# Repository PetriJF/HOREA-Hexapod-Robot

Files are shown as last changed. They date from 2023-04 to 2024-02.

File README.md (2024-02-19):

# ROS2 Hexapod (Major update coming up!!)
HOREA

## IMPORTANT: Code refactoring in progress

Hello everyone! Just letting you know that the code is currently being refactored for the robot. The Hardware design of the robot was simplified, making it easier to work with and even cheaper, and those changes need to be reflected into the walking model as well.
A quick list of some of the features in progress:
- [x] Dynamic Gait Switching
- [x] Leg Fault handling
- [ ] Gazebo integration (RViz is implemented, Gazebo comes next)
- [ ] Vision/LiDAR support (Progress was made but more is needed)
- [x] Better step feedback
- [x] Better femur design
- [x] Jumping
- [x] Enabling the hexapod to walk on 4 or 5 legs
- [ ] Enabling the hexapod to walk in a crawl state (reducing the profile widthwise for fitting into narrow spots)
- [x] A more efficient node communication method for the data heavy transfers
- [x] Battery support.
Once all of those are completed, the new update will be pushed and the repository will be cleaned.
Also, after this update, the project will move from an alpha-like phase to beta.

WHY NOT WORKING HERE?
Because I am using this version of the codebase for demos and project sharing. I don't want to add something that might be unstable or buggy here

WHEN WILL THE CHANGES BE UPLOADED?
My plan for it is to have the new hardware design uploaded by the end of December with the code changes required to run the software on it. All the other features should be online by late March 2024 when the private branch will be fully integrated with main.

SHOULD I BUILD THE CURRENT VERSION OF THE ROBOT?
Personally, I would say no, as the new version fixes a lot of the problems this iteration has. The new version will also be cheaper and easier to assemble and service! If you can't wait, email me at "jamespetri28@gmail.com" and we can work together for a quicker solution!

Thank you everyone,
James

## Project Description

As part of the Robotics and Intelligent Devices degree, in the final year a project has to be undertaken by each student.

For my final year project I chose to fully research, design and develeop a hexapod robot with the appropriate control strategy to traverse diffused terrain. I also wanted to apply best practices in order to maximize the quality of the robot while minimizing the price, as I would like to make it a good research and hobby platform for people to take and work with.

The Hexapod, named H.O.R.E.A., works on a raspberry Pi running ROS2 humble. It comes equipped with an IMU, for tilt correction, and a switch in each tibia, for leg feedback. With those two perception methods, the hexapod is fully prepared to undertake light to medium off-road challanges (Relative to the robot's size). Some metrics are available at the end.

In the future, the platform might add vision and a more robust control design in order to improve its capabilities even further.

## OPEN-SOURCE

Please note that the project is open-source, so feel free to fork it. I must mention that if you plan to work on the robot, please read the issues first as they might indicate a future feature I am working on that you might find useful. The project is work-in-progress, so it is worth checking it often for updates!

## CAD and 3D printing

The version current version of the hexapod is fully 3D printed in ABS, except for the TibiaTips, which are printed in TPU in order to provide more grip. Some images of the CAD assembly can be seen below

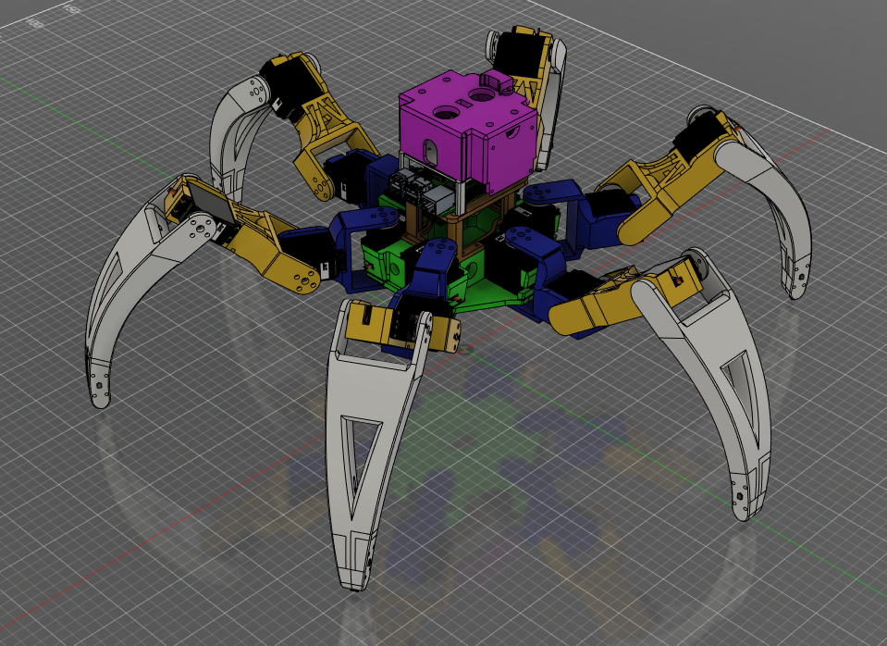
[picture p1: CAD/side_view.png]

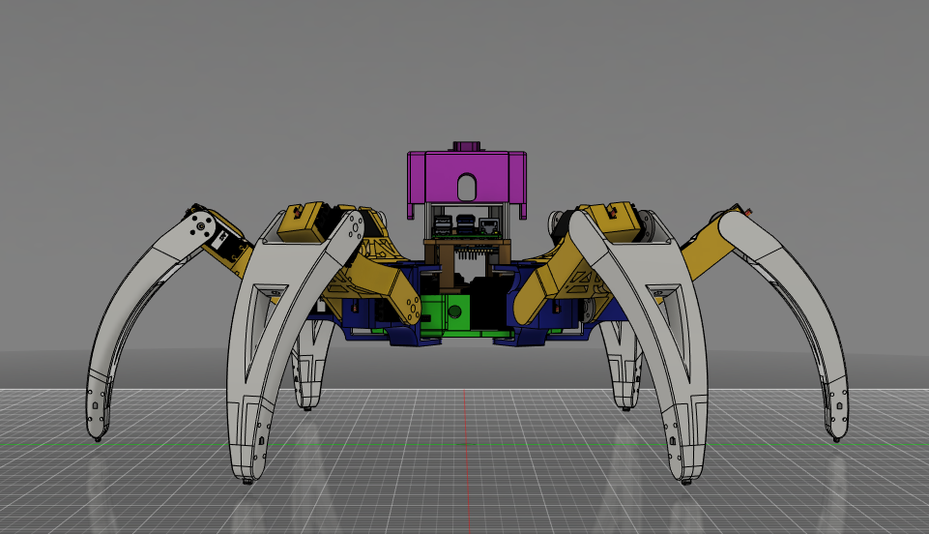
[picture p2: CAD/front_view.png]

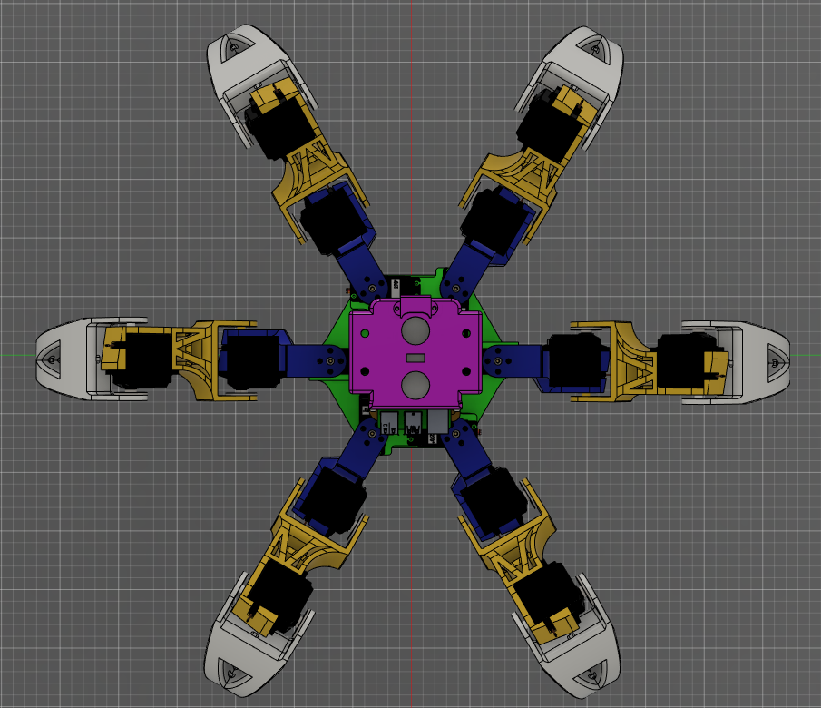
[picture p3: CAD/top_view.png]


## Codebase

The hexapod's codebase is designed to work with Ubuntu 22.04 Server and ROS2 Humble. I will not work on backwards compatibility with previous versions of ROS/Ubuntu. When cloning the repository, please ensure you properly install ROS2 Humble (do the talker listener demo to ensure so). Once cloned, go to the parent directory and build it.

```
colcon build
```

At the time of writing, there are 3 fully integrated run modes separated into launch files under hexapod_bringup. One of them is a keyboard controller, while the other two are gamepad controllers(one for generic style, and one for XBox style). The run procedure for the keyboard and XBox controllers can be seen below:

1. Keyboard TeleOp

    For this mode you will need to terminals. One for the launch file launching all the necessary nodes to run the robot and one for the keyboard TeleOp.

    Terminal 1:
    ```
    ros2 launch hexapod_bringup stdRun.launch.py
    ```
    Terminal 2:
    ```
    ros2 launch hexapod_controller teleop_keyboard_node
    ```

    On the second terminal a list of the controls will appear and you'll be able to control the robot similarly to the turtlesim teleop example in ROS2

2. Gamepad TeleOp (PS style controller)

    For this mode a single terminal is needed which initializes the robot and you can control the robot through a controller connected via USB or bluetooth. I recommend using a wireless controller with an USB dongle. The code for running in this mode:

    ```
    ros2 launch hexapod_bringup xBoxGamepadMode.launch.py
    ```

## Bill Of Materials

A full bill of materials can be found under the CAD directory. Look for "Full BOM.xlsx"

## When to expect a well rounded version?

By the start of June 2023 a full version with everything needed to build and use the robot will be released. The robot is currently in working order (08/05/2023), but some of the off-road features are on development branches. 

## Metrics

| Metric | Value |
| :---: | :---:|
|Weight | 2.68 Kg |
|Payload | 2.4 Kg |
|Maximum leg radius | 87 cm |
|Leg Reach | 37 cm |
|Robot Height | 17.6 cm (23.6 cm with  gamepad antenna) |
|Maximum dynamic incline (rough surface) | 23.5° |
|Maximum static incline (rough surface) | 35.3° |
|Maximum dynamic incline (smooth surface) | 10.3° |
|Maximum static incline (smooth surface) | 19.6° |
|Speed (Tripod gait) | 0.253 m/s |

## More pictures of H.O.R.E.A.

HOREA
HOREA
HOREA
HOREA
HOREA

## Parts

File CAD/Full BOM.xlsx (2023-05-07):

PART NUMBER | PART NAME | DESCRIPTION | QUANTITY | Link to Supplier | UNIT COST | AMOUNT
3769970 | DC-DC Buck Converter | A buck DC to DC converter that will be used to make the electrical voltages required for the robot | 3 | https://ie.farnell.com/dfrobot/dfr0205/dc-dc-power-module/dp/3769970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 | €9.62 | €28.86
1850634 | USB Connector | Usb connector for the circuit connecting the 5V power line to the raspberry pi | 1 | https://ie.farnell.com/multicomp/2ub3001-w05100/sealed-usb-2-0-type-a-receptacle/dp/1850634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 | €4.71 | €4.71
1850636 | USB Extender | Usb male to usb female that will be used to bring the usb port from the raspberry pi to the top side of the robot, enabling mounting the antenna for the gamepad controller vertically | 1 | https://ie.farnell.com/multicomp/2ub3001-w05101/adaptor-usb-type-a-jack-plug/dp/1850636 | €6.84 | €6.84
3287202 | USB C (At 90deg) to USB A | A cable used to neatly power the raspberry pi from the power board | 1 | https://ie.farnell.com/roline/11-02-9060/usb-cable-2-0-a-plug-c-plug-800mm/dp/3287202 | €12.30 | €12.30
3498526 | USB Extender | Another USB extender in case an USB drive is added or other periferals. Check alternative to the other one was chosen as this one is not mandatory | 1 | https://ie.farnell.com/pro-signal/psg91455/lead-usb2-0-a-male-a-female-white/dp/3498526 | €1.56 | €1.56
2507908 | DC Power connector female | Female input for powering the robot when on-wire running. Rated at 10.7A | 1 | https://ie.farnell.com/te-connectivity/1-2129458-2/dc-power-jack-10-7a-25vdc-black/dp/2507908 | €3.04 | €3.04
2507910 | DC Power connector male | Male output for powering the robot when on-wire running. Rated at 10.7A | 1 | https://ie.farnell.com/te-connectivity/1-2129334-1/dc-power-plug-10-7a-25vdc-yellow/dp/2507910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 | €3.41 | €3.41
1297215 | Cable sleeving | Cable sleeving to hide the motor cables at the robot. 10m at 15mm. | 1 | https://ie.farnell.com/pro-power/petbk15b10/sleeving-braid-15mm-black-10m/dp/1297215 | €12.78 | €12.78
1995-1000-ND | R4-2RS | Ball Bearing 6.35x11.55x4.98 mm | 18 | https://www.digikey.ie/en/products/detail/mechatronics-bearing-group/R4-2RS/9608359 | €1.61 | €28.98
1738-1231-ND | SER0019 Standard Servo | DSS-M15 -> metal geared standard servo | 18 | https://www.digikey.ie/en/products/detail/dfrobot/SER0019/7087128 | €16.03 | €288.54
1568-SEN-15335-ND | SEN-15335 | ICM-20948 Accelerometer, Gyroscope, Magnetometer Sensor Qwiic Platform Evaluation Expansion Board | 1 | https://www.digikey.ie/en/products/detail/sparkfun-electronics/SEN-15335/10279707?productid=10279707&gad=1 | €20.63 | €20.63
485-815 | Adafruit PCA9685 16x12 bit PWM controller | I2C PWM servo drivers. NOTE A capacitors has to be soldered into the marked slot on the PCB. With n being the servo count, the capacitor should have n * 100uF | 2 | https://www.mouser.ie/ProductDetail/Adafruit/815?qs=GURawfaeGuCGKbWyy9179Q%3D%3D | €14.05 | €28.10
SC0194 | Raspberry Pi 4 Model B | Raspberry Pi 4 Model B 4Gb. 2Gb should be fine if no vision is used. | 1 | https://thepihut.com/products/raspberry-pi-4-model-b?src=raspberrypi&variant=20064052740158 | €58.84 | €58.84
102656 | Raspberry Pi 4 Extreme Cooling Heat Sink Fan Kit | A heatsink for the raspberry pi with a fan included. | 1 | https://thepihut.com/products/raspberry-pi-4-extreme-cooling-heat-sink-fan-kit | €8.94 | €8.94
 |  | TOTAL PARTS | 51 |  | TOTAL | €507.52

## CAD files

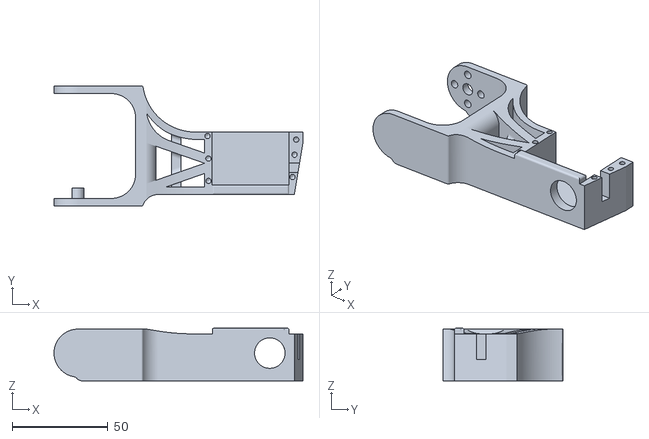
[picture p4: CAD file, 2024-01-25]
CAD/Femur.stl
129.8 x 62.6 x 27.5

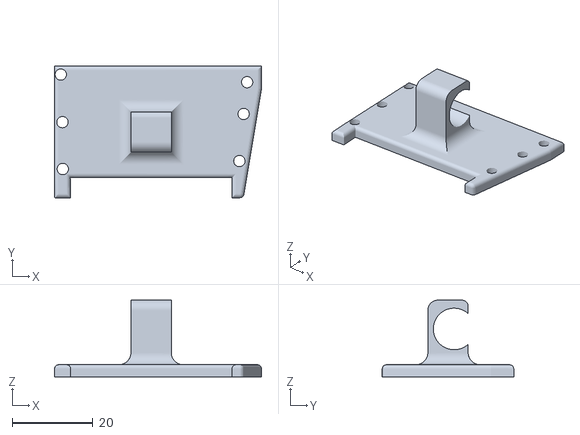
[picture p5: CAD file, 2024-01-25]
CAD/FemurLid.stl
51.3 x 32.6 x 19.0

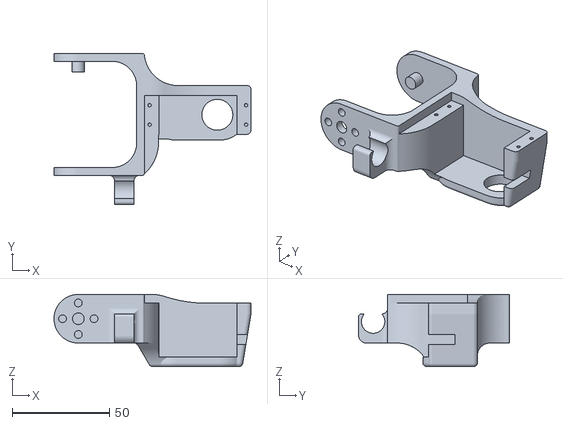
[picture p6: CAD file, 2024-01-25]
CAD/Coxa.stl
101.3 x 77.6 x 37.1

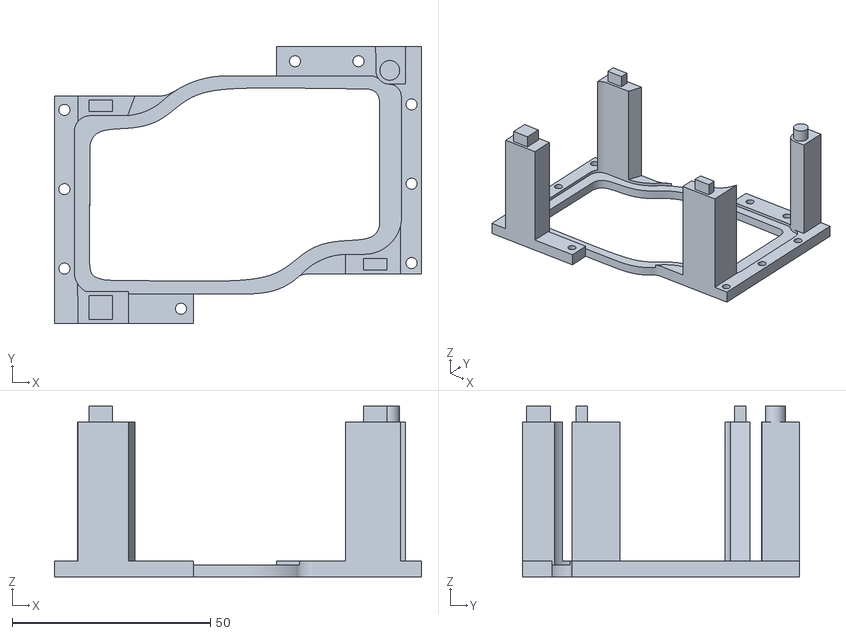
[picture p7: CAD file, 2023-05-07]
CAD/StackLifter.stl
92.5 x 69.8 x 43.0

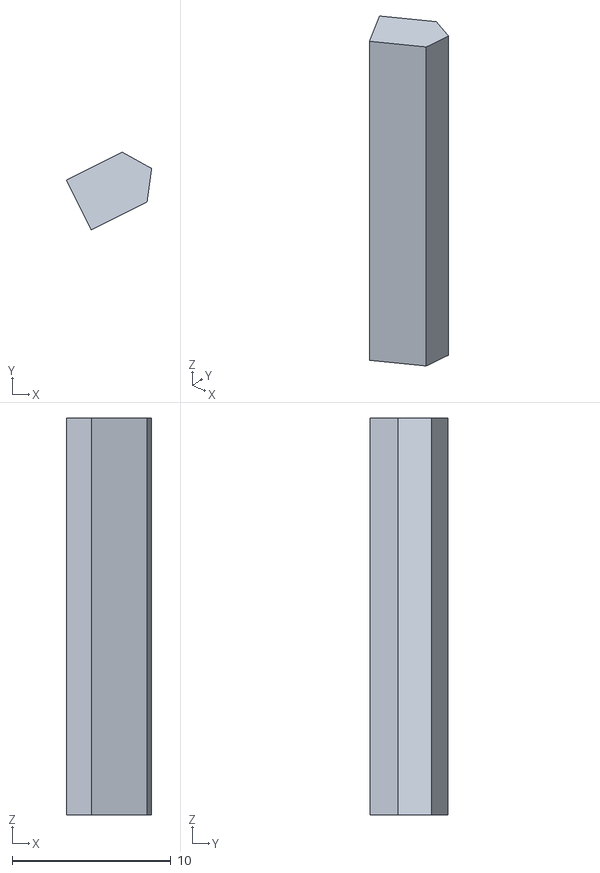
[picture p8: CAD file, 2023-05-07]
CAD/TibiaHoldingPin.stl
5.37 x 4.89 x 25.0

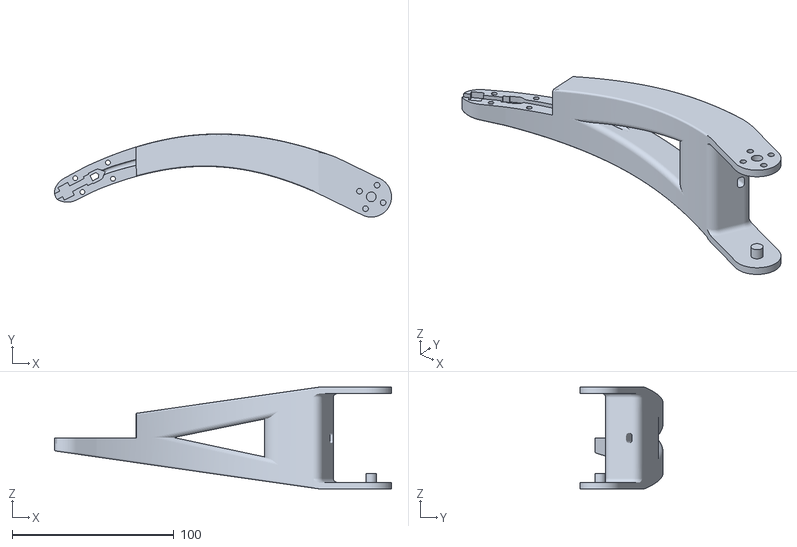
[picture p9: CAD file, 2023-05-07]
CAD/TibiaFrame.stl
208.2 x 51.4 x 62.8

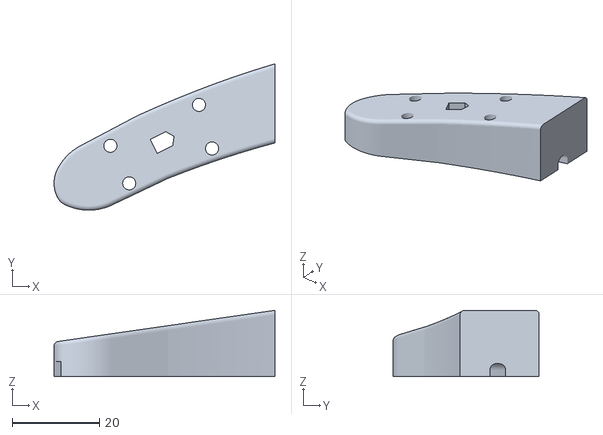
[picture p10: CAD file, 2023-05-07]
CAD/TibiaLid.stl
50.7 x 33.6 x 15.2

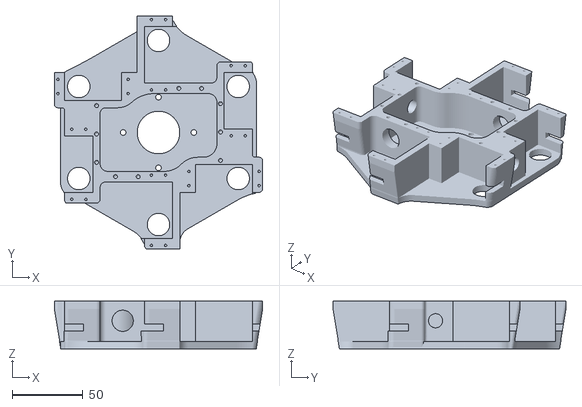
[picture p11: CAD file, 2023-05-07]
CAD/BasePlate.stl
147.2 x 164.6 x 33.6

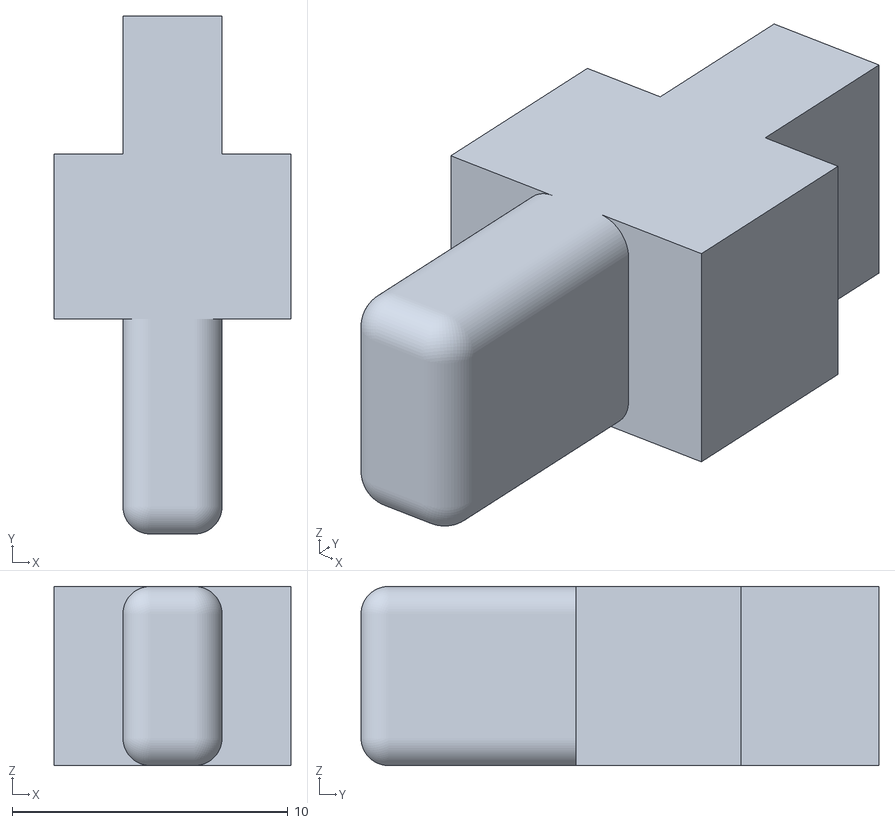
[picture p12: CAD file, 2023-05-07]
CAD/TibiaTip.stl
8.60 x 18.8 x 6.50

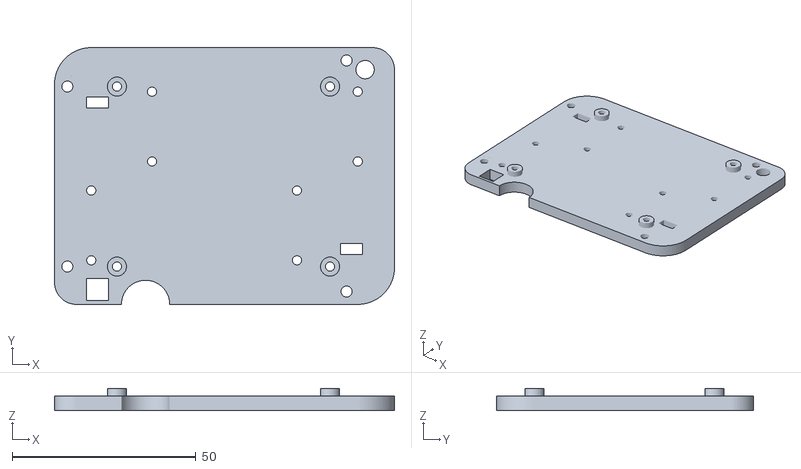
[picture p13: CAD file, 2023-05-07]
CAD/RaspStack.stl
92.5 x 69.9 x 6.00

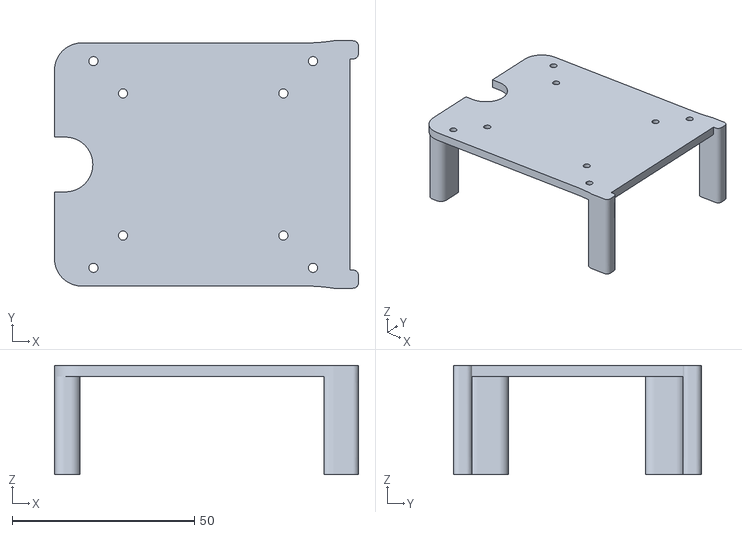
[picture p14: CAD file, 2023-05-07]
CAD/TopStack.stl
83.4 x 67.9 x 30.0

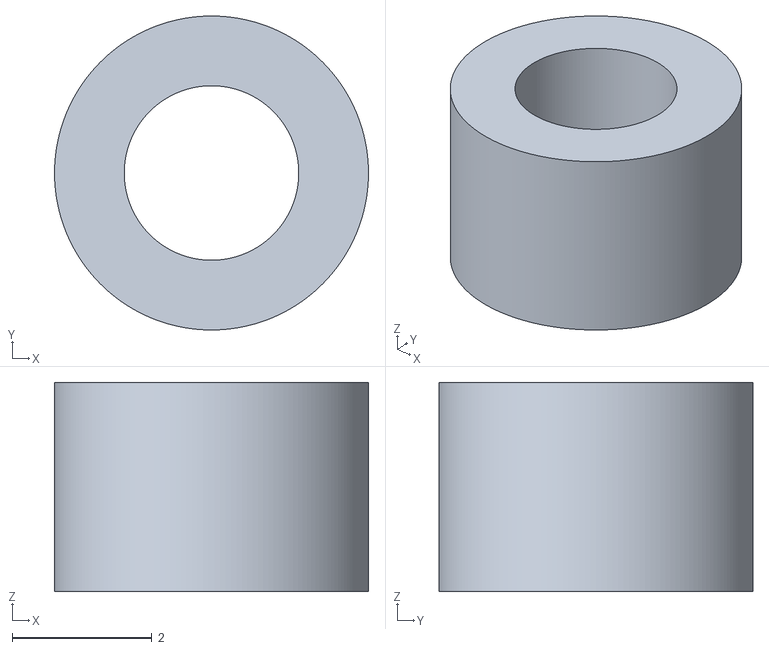
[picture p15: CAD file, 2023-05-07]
CAD/Spacer.stl
4.50 x 4.50 x 3.00

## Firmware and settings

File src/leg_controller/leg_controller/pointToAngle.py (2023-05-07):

import rclpy
from rclpy.node import Node
import numpy as np
from time import *
from hexapod_interfaces.msg import TargetAngles, TargetPositions
from std_msgs.msg import Float64MultiArray
from rcl_interfaces.msg import ParameterDescriptor
from geometry_msgs.msg import Point

class inverseKinematics(Node):    
    ## Node Constructor
    def __init__(self):
        # Initialize nodes
        super().__init__("kin_node")
        # Used for transmiting the servo target angles to the servo node
        self.targetAngles = TargetAngles()
        self.currentPos = TargetPositions()
        self.xAxisInclination = 0.0 
        self.yAxisInclination = 0.0
        self.ratio = 40.0

        # Declaring the robot design paramteres. Note 3 = PARAMETER_DOUBLE
        pd = ParameterDescriptor(description = "Robot Structure Description", type = 3) 
        self.declare_parameter(name = "coxa_len", descriptor = pd)
        self.declare_parameter(name = "femur_len", descriptor = pd)
        self.declare_parameter(name = "tibia_len", descriptor = pd)
        self.declare_parameter(name = "base_altitude", descriptor = pd)
        self.declare_parameter(name = "base_width", descriptor = pd)
        
        # Declaring the parameters representing each leg origin. Note 8 = PARAMETER_DOUBLE_ARRAY
        pd = ParameterDescriptor(description = "Origin definition for each leg", type = 8) 
        self.declare_parameter(name = "origin_RF", descriptor = pd)
        self.declare_parameter(name = "origin_RM", descriptor = pd)
        self.declare_parameter(name = "origin_RB", descriptor = pd)
        self.declare_parameter(name = "origin_LB", descriptor = pd)
        self.declare_parameter(name = "origin_LM", descriptor = pd)
        self.declare_parameter(name = "origin_LF", descriptor = pd)

        # Declaring the parameter representing the default orientation of each leg. Note 8 = PARAMETER_DOUBLE_ARRAY
        self.declare_parameter(name = "leg_angular_orientation", descriptor = pd)

        # Initializing the robot design variables from the parameters
        self.coxa_len_ = self.get_parameter("coxa_len").value
        self.femur_len_ = self.get_parameter("femur_len").value
        self.tibia_len_ = self.get_parameter("tibia_len").value
        self.base_altitude_ = self.get_parameter("base_altitude").value
        self.base_width_ = self.get_parameter("base_width").value


        # Initializing the origins from the parameters as point to make it more readable through the code.
        self.origin_RF_ = self.setPoint(self.get_parameter("origin_RF").value[0], self.get_parameter("origin_RF").value[1], 0.0)
        self.origin_RM_ = self.setPoint(self.get_parameter("origin_RM").value[0], self.get_parameter("origin_RM").value[1], 0.0)
        self.origin_RB_ = self.setPoint(self.get_parameter("origin_RB").value[0], self.get_parameter("origin_RB").value[1], 0.0)
        self.origin_LB_ = self.setPoint(self.get_parameter("origin_LB").value[0], self.get_parameter("origin_LB").value[1], 0.0)
        self.origin_LM_ = self.setPoint(self.get_parameter("origin_LM").value[0], self.get_parameter("origin_LM").value[1], 0.0)
        self.origin_LF_ = self.setPoint(self.get_parameter("origin_LF").value[0], self.get_parameter("origin_LF").value[1], 0.0)

        self.get_logger().info("Parameters declared and initialized successfully!")
        
        # Subscribing to the target potisions and publishing the target angles
        self.posSub = self.create_subscription(TargetPositions, 'HexLegPos', self.posCallback, 10)
        self.baseInclinationSub_ = self.create_subscription(Float64MultiArray, 'base_inclination', self.inclinationCallback, 10)
        self.angles = self.create_publisher(TargetAngles, 'HexAngles', 10)

        
        
        # Note gamma_ values : 0 RF, 1 RM, 2 RB, 3 LB, 4 LM, 5 LF 
        self.gamma_ = np.deg2rad(self.get_parameter("leg_angular_orientation").value)

        # Code used to make a rectangle with the leg. Used to test the accuracy of the kinematic model directly
        #sleep(15.0)
        
        #for leg_index in range(1, 6+1):
        #    self.targetAngles.shoulder_angle[leg_index] = 90.0
        #    self.targetAngles.hip_angle[leg_index] = 90.0
        #    self.targetAngles.knee_angle[leg_index] = 90.0

        #self.get_logger().info("cmd sent")
        #self.getLegAngles(self.setPoint(251.14, 145.0, 0.0), self.origin_RF_, 1)
        #self.angles.publish(self.targetAngles)
        #sleep(5.0)
        #self.getLegAngles(self.setPoint(301.14, 145.0, 0.0), self.origin_RF_, 1)
        #self.angles.publish(self.targetAngles)
        #sleep(5.0)
        #self.getLegAngles(self.setPoint(301.14, 205.0, 0.0), self.origin_RF_, 1)
        #self.angles.publish(self.targetAngles)
        #sleep(5.0)
        #self.getLegAngles(self.setPoint(251.14, 205.0, 0.0), self.origin_RF_, 1)
        #self.angles.publish(self.targetAngles)
        #sleep(5.0)
        #self.getLegAngles(self.setPoint(0.0, 300.0, 0.0), self.origin_RM_, 2)
        #self.getLegAngles(self.setPoint(-251.14, 145.0, 0.0), self.origin_RB_, 3)
        #self.getLegAngles(self.setPoint(-251.14, -145.0, 0.0), self.origin_LB_, 4)
        #self.getLegAngles(self.setPoint(0.0, -300.0, 0.0), self.origin_LM_, 5)
        #self.getLegAngles(self.setPoint(251.14, -145.0, 0.0), self.origin_LF_, 6, publish = True)


        

    ## Gets three values and makes them into a Point
    def setPoint(self, xT = float, yT = float, zT = float):
        tempPoint = Point()
        tempPoint.x = float(xT)
        tempPoint.y = float(yT)
        tempPoint.z = float(zT)
        
        return tempPoint

    ## This function takes the position subscription and publishes the computed angles
    def posCallback(self, hexPos = TargetPositions):
        self.currentPos = hexPos
        if hexPos.z_pos[0] != 0.0:
            self.base_altitude_ = hexPos.z_pos[0] 

        originSet = self.getPlanarOrigins(self.xAxisInclination, self.yAxisInclination)

        self.getLegAngles(self.setPoint(hexPos.x_pos[1], hexPos.y_pos[1], hexPos.z_pos[1]), originSet[0], 1)
        self.getLegAngles(self.setPoint(hexPos.x_pos[2], hexPos.y_pos[2], hexPos.z_pos[2]), originSet[1], 2)
        self.getLegAngles(self.setPoint(hexPos.x_pos[3], hexPos.y_pos[3], hexPos.z_pos[3]), originSet[2], 3)
        self.getLegAngles(self.setPoint(hexPos.x_pos[4], hexPos.y_pos[4], hexPos.z_pos[4]), originSet[3], 4)
        self.getLegAngles(self.setPoint(hexPos.x_pos[5], hexPos.y_pos[5], hexPos.z_pos[5]), originSet[4], 5)
        self.getLegAngles(self.setPoint(hexPos.x_pos[6], hexPos.y_pos[6], hexPos.z_pos[6]), originSet[5], 6)

        self.angles.publish(self.targetAngles)

    ## Function solving the inverse kinematic model for a given specific leg and point 
    def getLegAngles(self, point = Point, origin = Point, leg_index = int, publish = False):
        # Distance from the leg origin to the point in a planar view
        D = np.sqrt((point.x - origin.x) * (point.x - origin.x) + (point.y - origin.y) * (point.y - origin.y))
        # Distance without the coxa
        L = D - self.coxa_len_
        # Triangle height from the input point and the desired gait altitude
        # Note: The last term represents the tilt modification on the specific leg
        A = point.z - self.base_altitude_ - origin.z
        # Distance the origin to the tip of the leg
        Lprime = np.sqrt(A * A + L * L)
        
        # Get the step displacement from the home location
        T = np.sqrt((point.x - origin.x - D * np.cos(self.gamma_[leg_index - 1])) ** 2 + (point.y - origin.y -  D * np.sin(self.gamma_[leg_index - 1])) ** 2)
        # Get the shoulder angle relative to the middle line
        alphaPrime = np.rad2deg(np.arccos((2 * D * D - T * T) / (2 * D * D)))
        # Because cos is sign dependent, ro is used to determine on which side of the default line the leg goes
        ro = np.arccos(point.x / (np.sqrt(point.x * point.x + point.y * point.y)))
        if point.y < 0: # If we are working with legs from the left side of the robot, we must change the rotation direction and substract from 360
            ro = 2 * np.pi - ro
        # Based on the side of the point compared to the center rest position, add or substract from 90 alphaPrime, giving the final value of alpha
        alpha = 90.0 + (alphaPrime if (ro < self.gamma_[leg_index - 1]) else (-alphaPrime))
        # Line used to debug kinematic model.
        #self.get_logger().info(str(leg_index) + "->" + str(alpha) + " for " + str(point.x) + ", " + str(point.y) + " and " + str(origin.x) + " " + str(origin.y) + "\nD = " + str(D) + " T = " + str(T) + " aprim = " + str(alphaPrime))

        # (z, D) plane. x and y are projected on the D-plane
        delta = np.arcsin(L / Lprime)
        beta = np.arccos(self.limiter((self.tibia_len_ * self.tibia_len_ - self.femur_len_ * self.femur_len_ - Lprime * Lprime) / (-2.0 * self.femur_len_ * Lprime), -1.0, 1.0))
        sigma = np.arccos(self.limiter((Lprime * Lprime - self.femur_len_ * self.femur_len_ - self.tibia_len_ * self.tibia_len_) / (-2.0 * self.femur_len_ * self.tibia_len_), -1.0, 1.0))

        # There are two cases as the triangle switches side when the leg goes over the robot's base level
        tetha1 = self.limiter(180.0 - np.rad2deg(beta + delta) if point.z < self.base_altitude_ else np.rad2deg(delta - beta))
        tetha2 = self.limiter(90.0 + (180.0 - (np.rad2deg(sigma) + 45.0))) # Note that the 45 represents the assembly offset between the tibia and femur!

        # Setting the target angles for the leg the et_parinverse kinematics were computed for
        self.targetAngles.shoulder_angle[leg_index] = alpha
        self.targetAngles.hip_angle[leg_index] = tetha1
        self.targetAngles.knee_angle[leg_index] = tetha2

        # If we want to publish from here, publish must be set to true
        if (publish == True):
            self.angles.publish(self.targetAngles)

    ## Computes the origins of the legs based on the two inclination variables
    def getPlanarOrigins(self, xTilt = float, yTilt = float):
        return [
            self.getIndexPlanarOrigin(self.origin_RF_, xTilt, yTilt, 0),
            self.getIndexPlanarOrigin(self.origin_RM_, xTilt, yTilt, 1),
            self.getIndexPlanarOrigin(self.origin_RB_, xTilt, yTilt, 2),
            self.getIndexPlanarOrigin(self.origin_LB_, xTilt, yTilt, 3),
            self.getIndexPlanarOrigin(self.origin_LM_, xTilt, yTilt, 4),
            self.getIndexPlanarOrigin(self.origin_LF_, xTilt, yTilt, 5)
        ]
    
    def getIndexPlanarOrigin(self, origin = Point(), xTilt = float, yTilt = float, index = int):
        temp = Point()
        # ground plane 0 axis
        temp.x = origin.x * np.cos(yTilt) + yTilt * self.ratio
        # ground plane
        temp.y = origin.y * np.cos(xTilt) + xTilt * self.ratio
        # depth axis
        temp.z = origin.x * np.sin(yTilt) + origin.y * np.sin(xTilt)

        return temp

    ## Simple function to set the limits of the angles for the servos in order to not get out of bounds or to limit the servo movement. Also used to keep trig values within ranges
    def limiter(self, value, minLimit = 0.0, maxLimit = 180.0):
        if value > maxLimit:
            value = maxLimit
        if value < minLimit:
            value = minLimit

        return value

    def inclinationCallback(self, inclinations):
        self.xAxisInclination = inclinations.data[0] 
        self.yAxisInclination = inclinations.data[1]

        self.posCallback(self.currentPos)

def main(args = None):
    # Initialize the node
    rclpy.init(args = args)
    invKinNode = inverseKinematics()
    
    # Keep the node running
    try:
        rclpy.spin(invKinNode)
    except KeyboardInterrupt:
        pass

    invKinNode.destroy_node()
    # Stop the node
    rclpy.shutdown()

if __name__ == '__main__':
    main()

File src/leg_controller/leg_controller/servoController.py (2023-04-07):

#!/usr/bin/env python3
import rclpy
from rclpy.node import Node
from rcl_interfaces.msg import ParameterDescriptor
from time import *
from adafruit_servokit import ServoKit
from hexapod_interfaces.msg import TargetAngles

class hexMotorControl(Node):    
    def __init__(self):
        super().__init__("hex_legs_controller")

        # Defining a descriptor for all the legs. Note 7 = PARAMETER_INTEGER_ARRAY!
        pd = ParameterDescriptor(description = "Port Definitions for each leg", type = 7) 

        # Declaring the parameters
        self.declare_parameter(name = "LB", descriptor = pd)
        self.declare_parameter(name = "LM", descriptor = pd)
        self.declare_parameter(name = "LF", descriptor = pd)
        self.declare_parameter(name = "RF", descriptor = pd)
        self.declare_parameter(name = "RM", descriptor = pd)
        self.declare_parameter(name = "RB", descriptor = pd)

        # Initializing the parameters
        self.portsRF = self.get_parameter("RF").value
        self.portsRM = self.get_parameter("RM").value
        self.portsRB = self.get_parameter("RB").value
        self.portsLF = self.get_parameter("LF").value
        self.portsLM = self.get_parameter("LM").value
        self.portsLB = self.get_parameter("LB").value

        self.get_logger().info("Parameters declared and initialized successfully!")

        # Defining the servo controllers
        self.kitL = ServoKit(channels=16, address=66) # 41 in hex
        self.kitR = ServoKit(channels=16, address=65) # 42 in hex
        
        # Setting the PWM ranges for all the servos
        for i in range(0, 16):
            self.kitL.servo[i].set_pulse_width_range(500, 2500)
            self.kitR.servo[i].set_pulse_width_range(500, 2500)
        
        self.get_logger().info("Servo controllers initialized and servos configured!")

        self.angleSubscriber = self.create_subscription(TargetAngles, "HexAngles", self.anglesCallback, 10)
        self.get_logger().info("Servo Controller Subscriber running")

    # Callback from the subsciber. Takes the angles fromt the TargetAngles array and moves the servos to the specific angle
    def anglesCallback(self, angleHex = TargetAngles):
        self.setLegServoAngles(True, self.portsRF, angleHex.shoulder_angle[1], angleHex.hip_angle[1], angleHex.knee_angle[1])
        self.setLegServoAngles(True, self.portsRM, angleHex.shoulder_angle[2], angleHex.hip_angle[2], angleHex.knee_angle[2])
        self.setLegServoAngles(True, self.portsRB, angleHex.shoulder_angle[3], angleHex.hip_angle[3], angleHex.knee_angle[3])
        self.setLegServoAngles(False, self.portsLB, angleHex.shoulder_angle[4], angleHex.hip_angle[4], angleHex.knee_angle[4])
        self.setLegServoAngles(False, self.portsLM, angleHex.shoulder_angle[5], angleHex.hip_angle[5], angleHex.knee_angle[5])
        self.setLegServoAngles(False, self.portsLF, angleHex.shoulder_angle[6], angleHex.hip_angle[6], angleHex.knee_angle[6])


    def setLegServoAngles(self, side = bool, legPorts = [int, int, int], hipAngle=float, shoulderAngle=float, kneeAngle=float):
        if side == False:
            self.kitL.servo[legPorts[0]].angle = hipAngle
            self.kitL.servo[legPorts[1]].angle = shoulderAngle
            self.kitL.servo[legPorts[2]].angle = kneeAngle 

        elif side == True:
            self.kitR.servo[legPorts[0]].angle = hipAngle
            self.kitR.servo[legPorts[1]].angle = shoulderAngle
            self.kitR.servo[legPorts[2]].angle = kneeAngle 

def main(args = None):
    rclpy.init(args = args)
    
    # Node
    node = hexMotorControl()  # create a node 
    
    rclpy.spin(node) # keep node alive 

    # End Node
    try:
        rclpy.spin(node)
    except KeyboardInterrupt:
        pass
    node.destroy_node()
    rclpy.shutdown()

if __name__ == '__main__':
    main()

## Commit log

2023-01-23 Added demo directory. Added pwm rectification for servo
2023-01-24 Added the subscriber for the hexapod leg control
2023-01-30 Added the addressing for the 2 servo controllers. Left: 0x41, Right 0x42
2023-02-03 Fixed PWM ranges
2023-02-03 Added origin referencing for each leg
2023-02-03 Make the inverse kinematics node
2023-02-03 Commiting inverse kinematic node
2023-02-05 Fixed all errors regarding the publisher
    [pointToAngle.py]
2023-02-05 Fixed the bug. Wrong centering on servos
    [pointToAngle.py]
2023-02-06 Fixed bug caused by triangle switching sides when leg goes over the robot's gait level
    [pointToAngle.py]
2023-02-11 Added the directory for the hexapod CAD files
2023-02-11 Added the current version
    Added the current design for the robot.
    Uploaded in .stl format (for printing) and .f3d format (for editing in Fusion 360)
    Also added the full assembly for reference in .step format
    [Base_Plate_Tolerance v6.f3d, Base_Plate_Tolerance v6.stl, Coxa v2.f3d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]
2023-02-18 Added the new leg referencing interface
2023-02-19 Base framework for the tripod gait made
2023-02-27 Added the leg end effector trajectory planner with bezier curves
2023-02-27 Fixed bug where there is no difference between gait altitude and base altitude
    [pointToAngle.py]
2023-03-14 Added base framework for the sensehat sensory node
2023-03-14 Separated sense hat and sparkfun imus
2023-03-20 Added basic code to read from the IMU
2023-03-20 Added the direct leg controller node to the launch file
2023-03-20 interchanged i2c addressing
2023-03-20 fixed the ramifications of the i2c addressing missmatch
    [pointToAngle.py, simpleCommands.py]
2023-03-20 Fixed x and y coordinates for all leg controls
    [pointToAngle.py, simpleCommands.py]
2023-03-20 Added side dependency in the kinematic model
2023-03-22 Added an improved inverse kinematic model
2023-03-25 Made sure the nodes are properly shutdown to avoid memory leaks
    [motorControlDemo.py, pointToAngle.py, servoController.py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]
2023-03-28 Added a config file for the kinematics node
2023-03-28 Fully added the unit testing for the kinematic model using pytest
2023-03-28 Added two screenshots of the hexapod full assembly
2023-04-02 Did some quick test files for buttons to aid EE button dev
2023-04-08 Added quick tester for 6 buttons
2023-04-08 Fixed the base lowering
    [simpleCommands.py]
2023-04-14 Flipped inclination x-axis orientation
2023-05-07 updated CAD files
    [BasePlate.stl, Base_Plate_Tolerance v6.f3d, Base_Plate_Tolerance v6.stl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]
2023-05-07 Updated CAD snapshots and added BOM
    [Full BOM.xlsx]
